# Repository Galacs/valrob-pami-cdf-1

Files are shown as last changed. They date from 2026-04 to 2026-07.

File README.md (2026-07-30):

# Carte Pami CDF 1

Pami integrated circuit board with dual silent stepper driver and ToF sensor

## IC List

- ESP32-S3FH4R2 (Main MCU)
- LDL212 (MCU 3v3 LDO)
- BQ77905 (battery protection)
- WS2812B (RGB addressable led)
- MLT-5020 (buzzer)
- VL53L0X (ToF ranging sensor)
- 2x TMC2209 (Silent 3A stepper driver)

## Top preview

## Preview 3d render

## Pictures

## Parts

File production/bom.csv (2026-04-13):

Designator | Footprint | Quantity | Value | LCSC Part #
AE1 | Johanson_2450AT18x100 | 1 | Antenna | C127629
BZ1 | MagneticBuzzer_Huaneng_MLT-5020 | 1 | Buzzer | C94598
C1, C14, C15, C16, C17, C2, C49, C50 | 0805 | 8 | 10u | C440198
C10, C12, C20, C26, C27, C29, C3, C30, C31, C4, C47, C48, C5, C6, C7, C8, C9 | 0402 | 17 | 0u1 | C307331
C11, C13, C24, C28, C32, C33, C53, C54 | 0402 | 8 | 1u | C52923
C18, C19 | 0402 | 2 | 12p | C1547
C21, C34, C35, C37 | 0402 | 4 | 4u7 | C23733
C22, C23 | 0402 | 2 | 1p2 | C76899
C25 | 0402 | 1 | 10u | C15525
C36, C42 | 0402 | 2 | 22n | C1532
C39, C45 | CP_Elec_6.3x7.7 | 2 | 100u | C165974
D1 | LED_WS2812B_PLCC4_5.0x5.0mm_P3.2mm | 1 | WS2812B | C2874885
D10 | D_SOD-323 | 1 | 100 | C2128
D11 | D_SOD-123 | 1 | 16 | C19077429
D12, D13 | 0805 | 2 | GREEN | C2297
D14 | 0603 | 1 | WHITE | C2290
D15 | D_SOD-123 | 1 | BZT52B3V3 | C19077392
D3, D4, D6, D8 | Diode_DFN1006 | 4 | H5VU10U | C22395519
D5, D9 | D_SMA | 2 | D_Schottky | C22452
J2 | USB_C_Receptacle_HRO_TYPE-C-31-M-12 | 1 | USB_C_Receptacle_USB2.0_14P | C393939
J3 | AMASS_XT30PW-M_1x02_P2.50mm_Horizontal | 1 | Conn_01x02 | C431092
J5 | PinHeader_2x03_P2.54mm_Vertical | 1 | Conn_01x06
L1 | L_Sunlord_MWSA0402S | 1 | 3u3 | C167207
L2 | 0402 | 1 | 24n | C167472
L3 | 0402 | 1 | 6n8 | C77110
L5, L6 | 0402 | 2 | 2n7 | C77108
Q1, Q2 | Vishay_PowerPAK_1212-8_Single | 2 | Q_NMOS | C111309
Q3 | SOT-323_SC-70 | 1 | Q_NMOS | C28646265
R1, R2, R36, R5, R7 | 0402 | 5 | 1k | C11702
R10 | 0402 | 1 | 52k3 | C26982
R11, R14, R16, R17, R27, R29, R31, R34, R35, R40, R41, R42 | 0402 | 12 | 10k | C25744
R12, R22 | 0603 | 2 | 470k | C23178
R13, R20 | 0402 | 2 | 1M | C26083
R15, R18, R23, R25, R26, R3, R4 | 0402 | 7 | 5k1 | C25905
R19 | 0603 | 1 | 3M | C23156
R21 | 0402 | 1 | 510 | C25123
R24 | 0402 | 1 | 0 | C17168
R28 | 0603 | 1 | 1k8 | C4177
R30 | 0402 | 1 | 470 | C25117
R32, R33 | 0402 | 2 | 22 | C25092
R6, R9 | 0402 | 2 | 100 | C25076
R8 | 1206 | 1 | 10m/1W | C105362
SW2 | JST_XH_B2B-XH-A_1x02_P2.50mm_Vertical | 1 | SW_Push | C158012
SW3, SW4 | SW_SPST_TS-1088-xR020 | 2 | SW_Push | C720477
U1 | SOT-583-8 | 1 | TPS62933 | C3200405
U2 | TSSOP-20_4.4x6.5mm_P0.65mm | 1 | BQ77905 | C2866527
U3 | ST_VL53L1x | 1 | VL53L0CXV0DH1 | C91199
U4 | QFN-56-1EP_7x7mm_P0.4mm_EP4x4mm_ThermalVias | 1 | ESP32-S3FN8 | C3013940
U5 | DFN-6-1EP_2x2mm_P0.5mm_ST | 1 | LDL212PV33R | C2969892
U8, U9 | VQFN-28-1EP_5x5mm_P0.5mm_EP3.7x3.7mm_ThermalVias | 2 | TMC2209-LA | C2150710
Y1 | Crystal_SMD_2016-4Pin_2.0x1.6mm | 1 | 48M | C7206306

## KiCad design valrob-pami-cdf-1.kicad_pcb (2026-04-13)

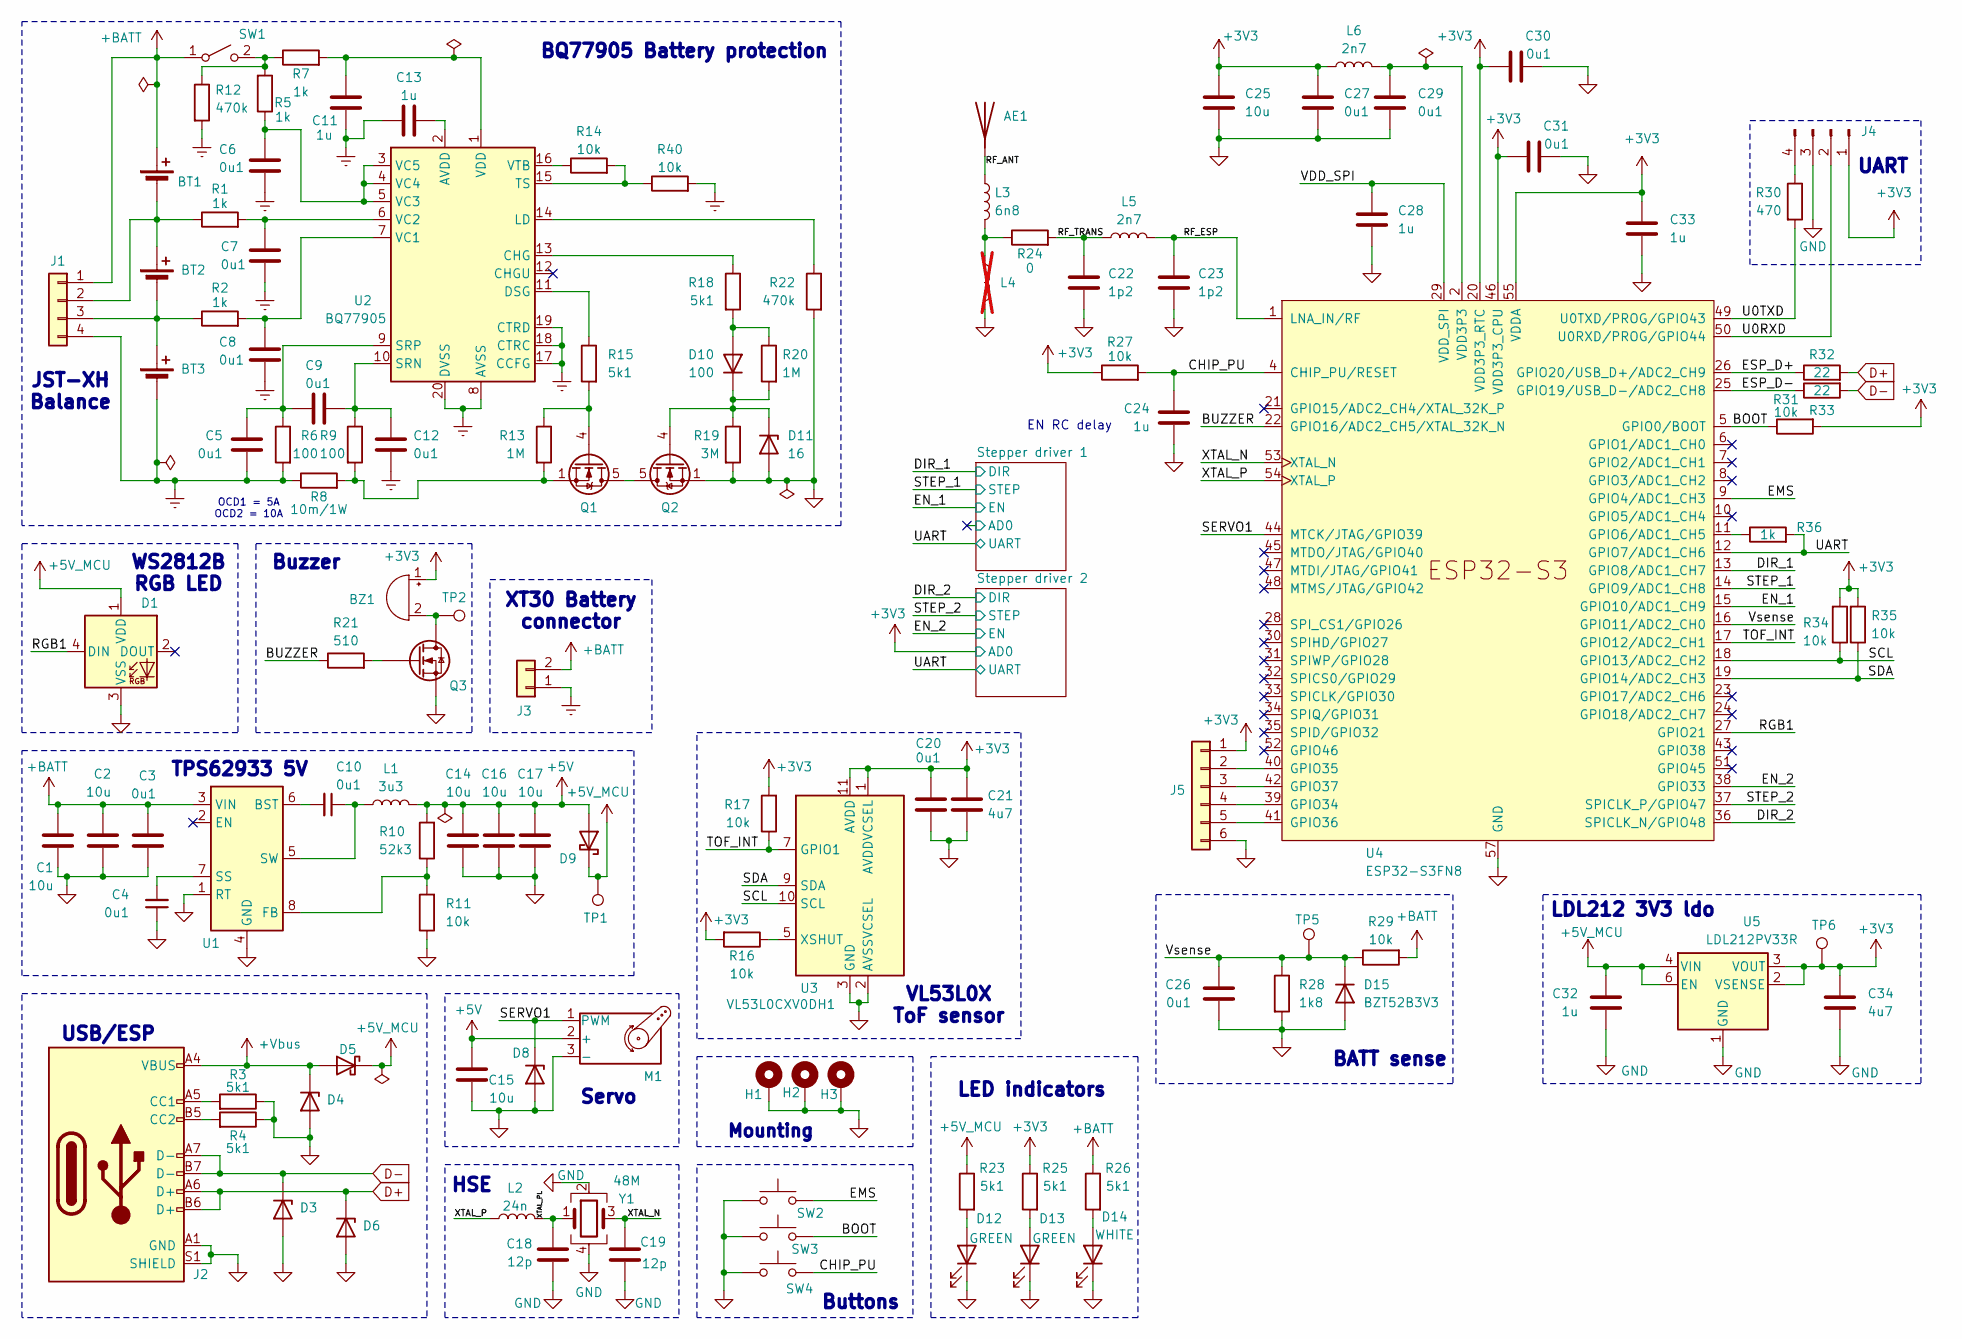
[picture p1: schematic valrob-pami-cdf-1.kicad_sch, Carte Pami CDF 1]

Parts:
AE1: Antenna; Johanson_2450AT18x100; Manufacturer Part Number RFANT3216120A5T; JLCPCB Part # C127629
BT1, BT2, BT3: Battery_Cell
BZ1: Buzzer; MagneticBuzzer_Huaneng_MLT-5020; Manufacturer Part Number MLT-5020; JLCPCB Part # C94598
C1, C2, C14, C15, C16, C17: 10u; C_0805_2012Metric; Manufacturer Part Number GRM21BR61H106KE43L; JLCPCB Part # C440198
C3, C4, C5, C6, C7, C8, C9, C10, C12, C20, C26, C27, C29, C30, C31: 0u1; C_0402_1005Metric; Manufacturer Part Number CL05B104KB54PNC; JLCPCB Part # C307331
C11, C13, C24, C28, C32, C33: 1u; C_0402_1005Metric; Manufacturer Part Number CL05A105KA5NQNC; JLCPCB Part # C52923
C18, C19: 12p; C_0402_1005Metric; Manufacturer Part Number 0402CG120J500NT; JLCPCB Part # C1547
C21, C34: 4u7; C_0402_1005Metric; Manufacturer Part Number CL05A475MP5NRNC; JLCPCB Part # C23733
C22, C23: 1p2; C_0402_1005Metric; Manufacturer Part Number GJM1555C1H1R2WB01D; JLCPCB Part # C76899
C25: 10u; C_0402_1005Metric; Manufacturer Part Number CL05A106MQ5NUNC; JLCPCB Part # C15525
D1: WS2812B; LED_WS2812B_PLCC4_5.0x5.0mm_P3.2mm; Manufacturer Part Number WS2812B-V5/W; JLCPCB Part # C2874885
D3, D4, D6, D8: H5VU10U; Diode_DFN1006; Manufacturer Part Number H5VU10U; JLCPCB Part # C22395519
D5, D9: D_Schottky; D_SMA; Manufacturer Part Number SS54; JLCPCB Part # C22452
D10: 100; D_SOD-323; Manufacturer Part Number 1N4148WS; JLCPCB Part # C2128
D11: 16; D_SOD-123; Manufacturer Part Number MMSZ5246B; JLCPCB Part # C19077429
D12, D13: GREEN; LED_0805_2012Metric; Manufacturer Part Number KT-0805G; JLCPCB Part # C2297
D14: WHITE; LED_0603_1608Metric; Manufacturer Part Number KT-0603W; JLCPCB Part # C2290
D15: BZT52B3V3; D_SOD-123; Manufacturer Part Number BZT52B3V3; JLCPCB Part # C19077392
H1, H2, H3: MountingHole_Pad; MountingHole_2.2mm_M2_Pad_Via
J1: Conn_01x04; JST_XH_S4B-XH-A_1x04_P2.50mm_Horizontal
J2: USB_C_Receptacle_USB2.0_14P; USB_C_Receptacle_HRO_TYPE-C-31-M-12; Manufacturer Part Number TYPE-C16PIN; JLCPCB Part # C393939
J3: Conn_01x02; AMASS_XT30PW-M_1x02_P2.50mm_Horizontal; Manufacturer Part Number XT30PW-M30.G.Y; JLCPCB Part # C431092
J4: Conn_01x04_Pin; PinHeader_1x04_P2.54mm_Vertical
J5: Conn_01x06; PinHeader_2x03_P2.54mm_Vertical
L1: 3u3; L_Sunlord_MWSA0402S; Manufacturer Part Number FXL0420-3R3-M; JLCPCB Part # C167207
L2: 24n; L_0402_1005Metric; Manufacturer Part Number LQW15AN24NG00D; JLCPCB Part # C167472
L3: 6n8; L_0402_1005Metric; Manufacturer Part Number LQG15HS6N8J02D; JLCPCB Part # C77110
L4: L; L_0402_1005Metric; not fitted
L5, L6: 2n7; L_0402_1005Metric; Manufacturer Part Number LQG15HS2N7S02D; JLCPCB Part # C77108
M1: Motor_Servo; PinHeader_1x03_P2.54mm_Horizontal
Q1, Q2: Q_NMOS; Vishay_PowerPAK_1212-8_Single; Manufacturer Part Number SIS412DN-T1-GE3; JLCPCB Part # C111309
Q3: Q_NMOS; SOT-323_SC-70; Manufacturer Part Number BSS138W; JLCPCB Part # C28646265
R1, R2, R5, R7, R36: 1k; R_0402_1005Metric; Manufacturer Part Number 0402WGF1001TCE; JLCPCB Part # C11702
R3, R4, R15, R18, R23, R25, R26: 5k1; R_0402_1005Metric; Manufacturer Part Number 0402WGF5101TCE; JLCPCB Part # C25905
R6, R9: 100; R_0402_1005Metric; Manufacturer Part Number 0402WGF1000TCE; JLCPCB Part # C25076
R8: 10m/1W; R_1206_3216Metric; Manufacturer Part Number FMF06FTHR010-LH; JLCPCB Part # C105362
R10: 52k3; R_0402_1005Metric; Manufacturer Part Number 0402WGF5232TCE; JLCPCB Part # C26982
R11, R14, R16, R17, R27, R29, R31, R34, R35, R40: 10k; R_0402_1005Metric; Manufacturer Part Number 0402WGF1002TCE; JLCPCB Part # C25744
R12, R22: 470k; R_0603_1608Metric; Manufacturer Part Number 0603WAF4703T5E; JLCPCB Part # C23178
R13, R20: 1M; R_0402_1005Metric; Manufacturer Part Number 0402WGF1004TCE; JLCPCB Part # C26083
R19: 3M; R_0603_1608Metric; Manufacturer Part Number 0603WAF3004T5E; JLCPCB Part # C23156
R21: 510; R_0402_1005Metric; Manufacturer Part Number 0402WGF5100TCE; JLCPCB Part # C25123
R24: 0; R_0402_1005Metric; Manufacturer Part Number 0402WGF0000TCE; JLCPCB Part # C17168
R28: 1k8; R_0603_1608Metric; Manufacturer Part Number 0603WAF1801T5E; JLCPCB Part # C4177
R30: 470; R_0402_1005Metric; Manufacturer Part Number 0402WGF4700TCE; JLCPCB Part # C25117
R32, R33: 22; R_0402_1005Metric; Manufacturer Part Number 0402WGF220JTCE; JLCPCB Part # C25092
SW1: SW_SPST; PinHeader_1x02_P2.54mm_Vertical
SW2: SW_Push; JST_XH_B2B-XH-A_1x02_P2.50mm_Vertical; Manufacturer Part Number B2B-XH-A(LF)(SN); JLCPCB Part # C158012
SW3, SW4: SW_Push; SW_SPST_TS-1088-xR020; Manufacturer Part Number TS-1088-AR02016; JLCPCB Part # C720477
TP1, TP2, TP5, TP6: TestPoint; TestPoint_Pad_D2.0mm
U1: TPS62933; SOT-583-8; Manufacturer Part Number TPS62933DRLR; JLCPCB Part # C3200405
U2: BQ77905; TSSOP-20_4.4x6.5mm_P0.65mm; Manufacturer Part Number BQ7790509PWR; JLCPCB Part # C2866527
U3: VL53L0CXV0DH1; ST_VL53L1x; Manufacturer Part Number VL53L0CXV0DH/1; JLCPCB Part # C91199
U4: ESP32-S3FN8; QFN-56-1EP_7x7mm_P0.4mm_EP4x4mm_ThermalVias; Manufacturer Part Number ESP32-S3FH4R2; JLCPCB Part # C3013940
U5: LDL212PV33R; DFN-6-1EP_2x2mm_P0.5mm_ST; Manufacturer Part Number LDL212PV33R; JLCPCB Part # C2969892
Y1: 48M; Crystal_SMD_2016-4Pin_2.0x1.6mm; Manufacturer Part Number R940000096; JLCPCB Part # C7206306

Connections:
+3V3: BZ1.1 (+), C20.1, C21.1, C25.1, C27.1, C30.1, C31.1, C33.1, C34.1, J4.1, J5.1, L6.1, R16.2, R17.2, R25.1, R27.1, R31.2, R34.2, R35.2, TP6.1 (1_1), U3.1 (AVDDVCSEL), U3.11 (AVDD), U4.20 (VDD3P3_RTC), U4.46 (VDD3P3_CPU), U4.55 (VDDA), U4.56 (VDDA), U5.2 (VSENSE), U5.3 (VOUT); also elsewhere on the board
+5V: C14.1, C15.1, C16.1, C17.1, D9.2 (A), L1.2, M1.2 (+), R10.2
+5V_MCU: C32.1, D1.1 (VDD), D5.1 (K), D9.1 (K), R23.1, TP1.1 (1_1), U5.4 (VIN), U5.6 (EN)
+BATT: BT1.1 (+), C1.1, C2.1, C3.1, J1.1, J3.2, R26.1, R29.2, SW1.1 (A), U1.3 (VIN); also elsewhere on the board
+Vbus: D4.1 (K), D5.2 (A), J2.A4 (VBUS), J2.A9 (VBUS), J2.B4 (VBUS), J2.B9 (VBUS)
/BOOT: R31.1, SW3.2, U4.5 (GPIO0/BOOT)
/BUZZER: R21.1, U4.22 (GPIO16/ADC2_CH5/XTAL_32K_N)
/CHIP_PU: C24.1, R27.2, SW4.2, U4.4 (CHIP_PU/RESET)
/DIR_1: U4.13 (GPIO8/ADC1_CH7); also elsewhere on the board
/DIR_2: U4.36 (SPICLK_N/GPIO48); also elsewhere on the board
/EMS: SW2.2, U4.9 (GPIO4/ADC1_CH3)
/EN_1: U4.15 (GPIO10/ADC1_CH9); also elsewhere on the board
/EN_2: U4.38 (GPIO33); also elsewhere on the board
/ESP_D+: R32.1, U4.26 (GPIO20/USB_D+/ADC2_CH9)
/ESP_D-: R33.1, U4.25 (GPIO19/USB_D-/ADC2_CH8)
/RF_ANT: AE1.1 (A_1), L3.1
/RF_ESP: C23.1, L5.2, U4.1 (LNA_IN/RF)
/RF_TRANS: C22.1, L5.1, R24.2
/RGB1: D1.4 (DIN), U4.27 (GPIO21)
/SCL: R34.1, U3.10 (SCL), U4.18 (GPIO13/ADC2_CH2)
/SDA: R35.1, U3.9 (SDA), U4.19 (GPIO14/ADC2_CH3)
/SERVO1: D8.1 (K), M1.1 (PWM), U4.44 (MTCK/JTAG/GPIO39)
/STEP_1: U4.14 (GPIO9/ADC1_CH8); also elsewhere on the board
/STEP_2: U4.37 (SPICLK_P/GPIO47); also elsewhere on the board
/TOF_INT: R17.1, U3.7 (GPIO1), U4.17 (GPIO12/ADC2_CH1)
/U0RXD: J4.2, U4.50 (U0RXD/PROG/GPIO44)
/U0TXD: R30.2, U4.49 (U0TXD/PROG/GPIO43)
/UART: R36.2, U4.12 (GPIO7/ADC1_CH6); also elsewhere on the board
/VDD_SPI: C28.1, U4.29 (VDD_SPI)
/Vsense: C26.1, D15.1 (K), R28.1, R29.1, TP5.1 (1_1), U4.16 (GPIO11/ADC2_CH0)
/XTAL_N: C19.1, U4.53 (XTAL_N), Y1.3
/XTAL_P: L2.1, U4.54 (XTAL_P)
/XTAL_PL: C18.2, L2.2, Y1.1
BGND: BT3.2 (-), C5.2, C6.2, C7.2, C8.2, C11.1, C12.2, C13.2, J1.4, J3.1, R6.2, R8.1, R12.2, R40.2, U2.8 (AVSS), U2.17 (CCFG), U2.18 (CTRC), U2.19 (CTRD), U2.20 (DVSS)
D+: D6.1 (K), J2.A6 (D+), J2.B6 (D+), R32.2
D-: D3.1 (K), J2.A7 (D-), J2.B7 (D-), R33.2
GND: C1.2, C2.2, C3.2, C4.1, C14.2, C15.2, C16.2, C17.2, C18.1, C19.2, C20.2, C21.2, C22.2, C23.2, C24.2, C25.2, C26.2, C27.2, C28.2, C29.2, C30.2, C31.2, C32.2, C33.2, C34.2, D1.3 (VSS), D3.2 (A), D4.2 (A), D6.2 (A), D8.2 (A), D11.2 (A), D12.1 (K), D13.1 (K), D14.1 (K), D15.2 (A), H1.1 (1_1), H2.1 (1_1), H3.1 (1_1), J2.A1 (GND), J2.A12 (GND), J2.B1 (GND), J2.B12 (GND), J2.S1 (SHIELD), J4.3, J5.6, L4.2, M1.3 (-), Q2.1 (S), Q2.2 (S), Q2.3 (S), Q3.2 (S), R3.1, R4.1, R11.1, R19.2, R22.2, R28.2, SW2.1, SW3.1, SW4.1, U1.1 (RT), U1.4 (GND), U3.2 (AVSSVCSEL), U3.3 (GND), U3.4 (GND), U3.6 (GND), U3.12 (GND), U4.57 (GND), U5.1 (GND), Y1.2, Y1.4; also elsewhere on the board
unnamed: BZ1.2 (-), Q3.3 (D), TP2.1 (1_1)
unnamed: D10.2 (A), R18.2, R20.1
unnamed: D10.1 (K), D11.1 (K), Q2.4 (G), R19.1, R20.2
unnamed: D12.2 (A), R23.2
unnamed: D13.2 (A), R25.2
unnamed: D14.2 (A), R26.2
unnamed: BT1.2 (-), BT2.1 (+), J1.2, R1.1
unnamed: BT2.2 (-), BT3.1 (+), J1.3, R2.1
unnamed: J2.A5 (CC1), R3.2
unnamed: J2.B5 (CC2), R4.2
unnamed: J4.4, R30.1
unnamed: J5.2, U4.40 (GPIO35)
unnamed: J5.3, U4.42 (GPIO37)
unnamed: J5.4, U4.39 (GPIO34)
unnamed: J5.5, U4.41 (GPIO36)
unnamed: L3.2, L4.1, R24.1
unnamed: Q1.5 (D), Q2.5 (D)
unnamed: Q1.4 (G), R13.1, R15.2
unnamed: Q1.1 (S), Q1.2 (S), Q1.3 (S), R8.2, R9.2, R13.2
unnamed: Q3.1 (G), R21.2
unnamed: R5.2, R7.1, R12.1, SW1.2 (B)
unnamed: C10.2, U1.6 (BST)
unnamed: R10.1, R11.2, U1.8 (FB)
unnamed: C4.2, U1.7 (SS)
unnamed: C10.1, L1.1, U1.5 (SW)
unnamed: C13.1, U2.2 (AVDD)
unnamed: R18.1, U2.13 (CHG)
unnamed: R15.1, U2.11 (DSG)
unnamed: R22.1, U2.14 (LD)
unnamed: C9.1, C12.1, R9.1, U2.10 (SRN)
unnamed: C5.1, C9.2, R6.1, U2.9 (SRP)
unnamed: R14.2, R40.1, U2.15 (TS)
unnamed: C8.1, R2.2, U2.7 (VC1)
unnamed: C7.1, R1.2, U2.6 (VC2)
unnamed: C6.1, R5.1, U2.3 (VC5), U2.4 (VC4), U2.5 (VC3)
unnamed: C11.2, R7.2, U2.1 (VDD)
unnamed: R14.1, U2.16 (VTB)
unnamed: R16.1, U3.5 (XSHUT)
unnamed: R36.1, U4.11 (GPIO6/ADC1_CH5)
VDD3P3: C29.1, L6.2, U4.2 (VDD3P3), U4.3 (VDD3P3)

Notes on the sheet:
UART
Buttons
LDL212 3V3 ldo
OCD1 = 5A OCD2 = 10A
JST-XH Balance
BQ77905 Battery protection
Servo
VL53L0X ToF sensor
EN RC delay
BATT sense
WS2812B RGB LED
LED indicators
Buzzer
TPS62933 5V
HSE
USB/ESP
XT30 Battery connector
Mounting

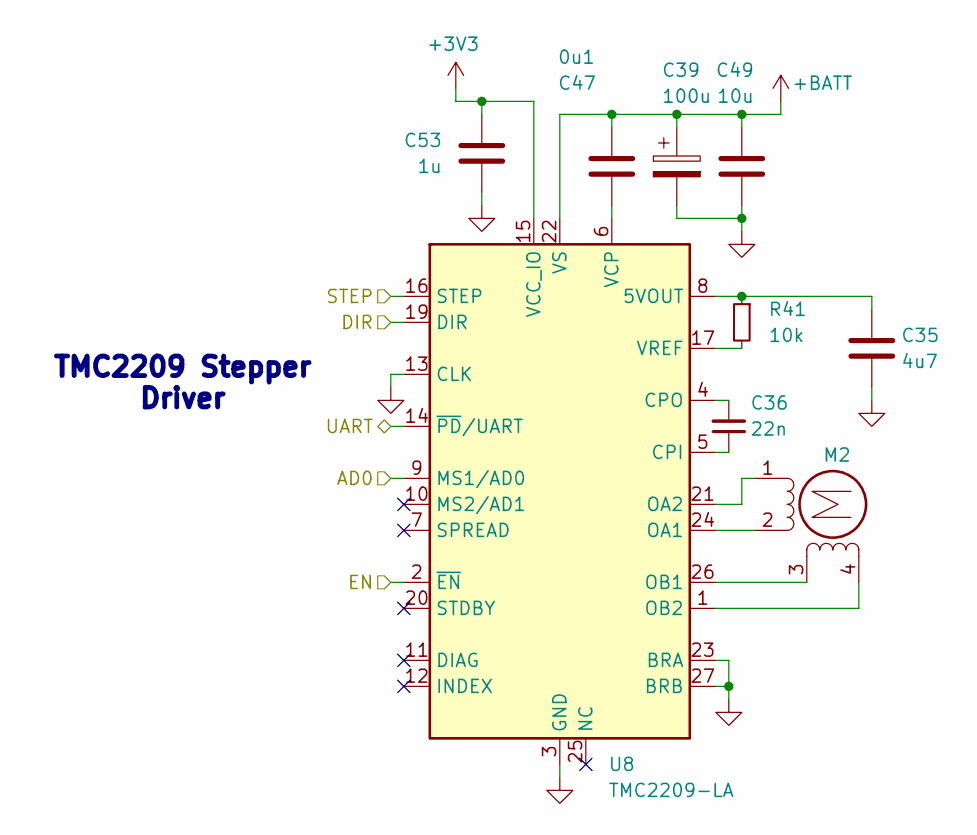
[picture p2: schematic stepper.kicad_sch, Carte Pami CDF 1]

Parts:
C35: 4u7; C_0402_1005Metric; Manufacturer Part Number CL05A475MP5NRNC; JLCPCB Part # C23733
C36: 22n; C_0402_1005Metric; Manufacturer Part Number 0402B223K500NT; JLCPCB Part # C1532
C39: 100u; CP_Elec_6.3x7.7; Manufacturer Part Number EEEFTH101XAP; JLCPCB Part # C165974
C47: 0u1; C_0402_1005Metric; Manufacturer Part Number CL05B104KB54PNC; JLCPCB Part # C307331
C49: 10u; C_0805_2012Metric; Manufacturer Part Number GRM21BR61H106KE43L; JLCPCB Part # C440198
C53: 1u; C_0402_1005Metric; Manufacturer Part Number CL05A105KA5NQNC; JLCPCB Part # C52923
M2: Stepper_Motor_bipolar; JST_XH_S4B-XH-A_1x04_P2.50mm_Horizontal
R41: 10k; R_0402_1005Metric; Manufacturer Part Number 0402WGF1002TCE; JLCPCB Part # C25744
U8: TMC2209-LA; VQFN-28-1EP_5x5mm_P0.5mm_EP3.7x3.7mm_ThermalVias; Manufacturer Part Number TMC2209-LA-T; JLCPCB Part # C2150710

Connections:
+3V3: C53.1, U8.15 (VCC_IO); also elsewhere on the board
+BATT: C39.1, C47.1, C49.1, U8.22 (VS), U8.28 (VS); also elsewhere on the board
/DIR_1: U8.19 (DIR); also elsewhere on the board
/EN_1: U8.2 (~EN); also elsewhere on the board
/STEP_1: U8.16 (STEP); also elsewhere on the board
/Stepper driver 1/AD0: U8.9 (MS1/AD0)
/UART: U8.14 (~PD/UART); also elsewhere on the board
GND: C35.2, C39.2, C49.2, C53.2, U8.3 (GND), U8.13 (CLK), U8.18 (GND), U8.23 (BRA), U8.27 (BRB), U8.29 (GND); also elsewhere on the board
unnamed: M2.1 (-_1), U8.21 (OA2)
unnamed: C35.1, R41.1, U8.8 (5VOUT)
unnamed: C36.1, U8.5 (CPI)
unnamed: C36.2, U8.4 (CPO)
unnamed: M2.2, U8.24 (OA1)
unnamed: M2.3, U8.26 (OB1)
unnamed: M2.4, U8.1 (OB2)
unnamed: C47.2, U8.6 (VCP)
unnamed: R41.2, U8.17 (VREF)

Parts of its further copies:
C37: 4u7; C_0402_1005Metric; Manufacturer Part Number CL05A475MP5NRNC; JLCPCB Part # C23733
C42: 22n; C_0402_1005Metric; Manufacturer Part Number 0402B223K500NT; JLCPCB Part # C1532
C45: 100u; CP_Elec_6.3x7.7; Manufacturer Part Number EEEFTH101XAP; JLCPCB Part # C165974
C48: 0u1; C_0402_1005Metric; Manufacturer Part Number CL05B104KB54PNC; JLCPCB Part # C307331
C50: 10u; C_0805_2012Metric; Manufacturer Part Number GRM21BR61H106KE43L; JLCPCB Part # C440198
C54: 1u; C_0402_1005Metric; Manufacturer Part Number CL05A105KA5NQNC; JLCPCB Part # C52923
M3: Stepper_Motor_bipolar; JST_XH_S4B-XH-A_1x04_P2.50mm_Horizontal
R42: 10k; R_0402_1005Metric; Manufacturer Part Number 0402WGF1002TCE; JLCPCB Part # C25744
U9: TMC2209-LA; VQFN-28-1EP_5x5mm_P0.5mm_EP3.7x3.7mm_ThermalVias; Manufacturer Part Number TMC2209-LA-T; JLCPCB Part # C2150710

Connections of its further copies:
+3V3: C54.1, U9.9 (MS1/AD0), U9.15 (VCC_IO); also elsewhere on the board
+BATT: C45.1, C48.1, C50.1, U9.22 (VS), U9.28 (VS); also elsewhere on the board
/DIR_2: U9.19 (DIR); also elsewhere on the board
/EN_2: U9.2 (~EN); also elsewhere on the board
/STEP_2: U9.16 (STEP); also elsewhere on the board
/UART: U9.14 (~PD/UART); also elsewhere on the board
GND: C37.2, C45.2, C50.2, C54.2, U9.3 (GND), U9.13 (CLK), U9.18 (GND), U9.23 (BRA), U9.27 (BRB), U9.29 (GND); also elsewhere on the board
unnamed: M3.1 (-_1), U9.21 (OA2)
unnamed: C37.1, R42.1, U9.8 (5VOUT)
unnamed: C42.1, U9.5 (CPI)
unnamed: C42.2, U9.4 (CPO)
unnamed: M3.2, U9.24 (OA1)
unnamed: M3.3, U9.26 (OB1)
unnamed: M3.4, U9.1 (OB2)
unnamed: C48.2, U9.6 (VCP)
unnamed: R42.2, U9.17 (VREF)

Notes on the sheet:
TMC2209 Stepper Driver

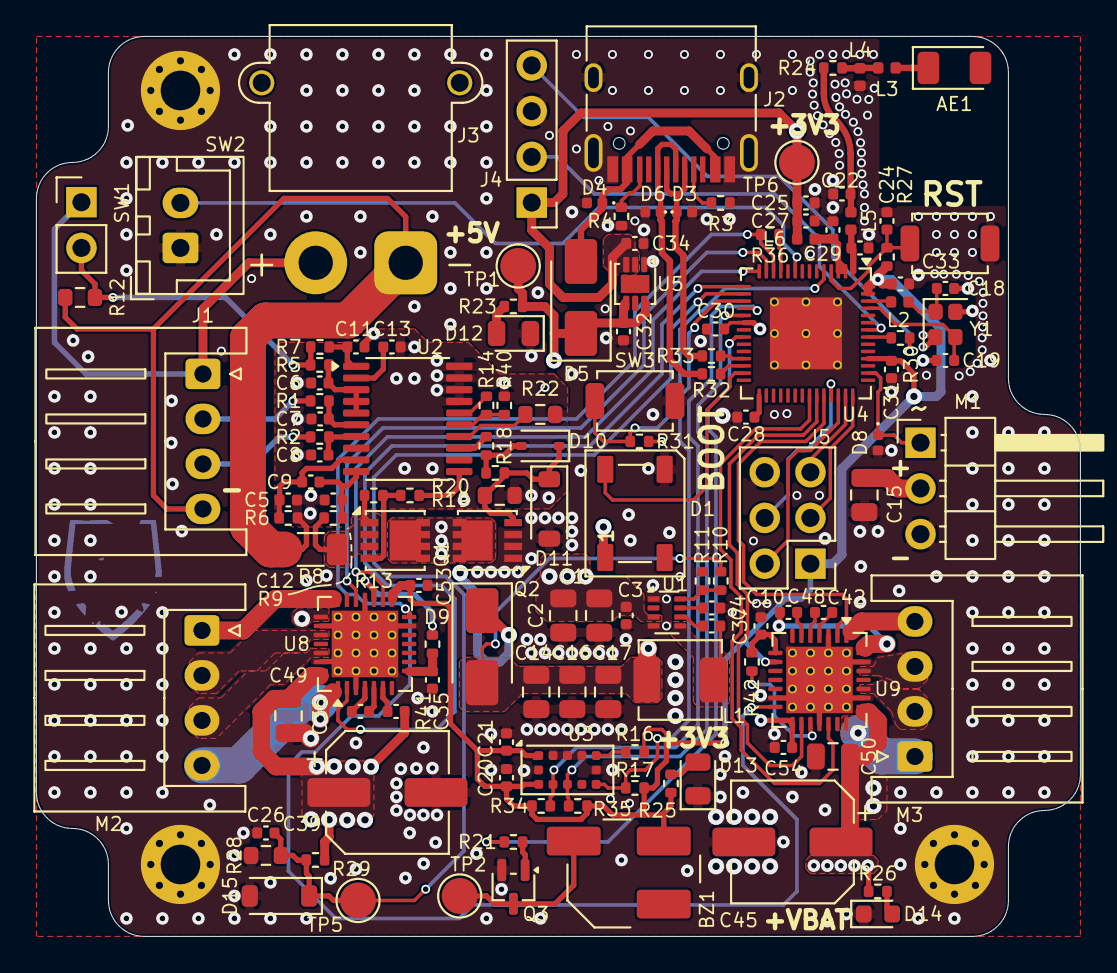
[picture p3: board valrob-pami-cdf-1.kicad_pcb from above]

Board: 4 copper layers, 58.0 x 50.0 mm, 136 parts (0 on the bottom side), 95 nets.

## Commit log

2026-02-16 schem: import esp32-s3 circuit from mhadb-main-board
    [valrob-pami-cdf-1.kicad_sch]
2026-02-16 schem: import HSE crystal
    [valrob-pami-cdf-1.kicad_sch]
2026-02-16 schem: import usbc connector
    [valrob-pami-cdf-1.kicad_sch]
2026-02-16 schem: import LDL212 3V3 ldo
    [valrob-pami-cdf-1.kicad_sch]
2026-02-16 schem: add BOOT and CHIP_PU buttons*
    [valrob-pami-cdf-1.kicad_sch]
2026-02-16 schem: add 3x WS2812B RGB LEDs
    [valrob-pami-cdf-1.kicad_sch]
2026-02-16 schem: add servo connector
    [valrob-pami-cdf-1.kicad_sch]
2026-02-16 schem: import BQ77905 Battery protection
    [valrob-pami-cdf-1.kicad_sch]
2026-02-16 schem: import buzzer
    [valrob-pami-cdf-1.kicad_sch]
2026-02-16 schem: add XT30 battery connector
    [valrob-pami-cdf-1.kicad_sch]
2026-02-16 pcb: add indicator leds
    [valrob-pami-cdf-1.kicad_sch]
2026-02-16 schem: add BQ77905 enable pull down resistor
    [valrob-pami-cdf-1.kicad_sch]
2026-02-16 schem: import DRV8424 stepper driver and reorganize
    [stepper.kicad_sch, valrob-pami-cdf-1.kicad_sch]
2026-02-16 schem: add placeholder TPS56A37 5V smps
    [valrob-pami-cdf-1.kicad_sch]
2026-02-16 schem: import BATT sense from valrob-alim
    [valrob-pami-cdf-1.kicad_sch]
2026-02-18 schem: add missing rgb leds ground symbol
    [valrob-pami-cdf-1.kicad_sch]
2026-02-20 schem: set stepper driver microstepping and decay config
    [stepper.kicad_sch]
2026-02-20 schem: change stepper driver connector
    [stepper.kicad_sch]
2026-02-20 schem: fix stepper hierachical sheets
    [stepper.kicad_sch, valrob-pami-cdf-1.kicad_sch]
2026-02-21 schem: change buck converter to TPS62933 5V
    [valrob-pami-cdf-1.kicad_sch]
2026-02-21 schem: add VL53L0x tof sensor
    [valrob-pami-cdf-1.kicad_sch]
2026-02-22 schem: add EMS button
    [valrob-pami-cdf-1.kicad_sch]
2026-02-22 schem: add mounting holes
    [valrob-pami-cdf-1.kicad_sch]
2026-02-22 schem: connecto all gpios to mcu
    [stepper.kicad_sch, valrob-pami-cdf-1.kicad_sch]
2026-02-22 schem: add test points
    [valrob-pami-cdf-1.kicad_sch]
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2026-02-22 schem: run and fix ERC
    [valrob-pami-cdf-1.kicad_sch]
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2026-02-22 schem: fix BOM
    [valrob-pami-cdf-1.kicad_sch]
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2026-02-22 schem: change rgb led 5v rail
    [valrob-pami-cdf-1.kicad_sch]
2026-02-22 pcb: import 4 layer stackup and constraints
    [valrob-pami-cdf-1.kicad_pcb]
2026-02-22 pcb: import components and add missing 3d models
    [valrob-pami-cdf-1.kicad_pcb]
2026-02-22 pcb: add stepper layout
    [stepper.kicad_sch, valrob-pami-cdf-1.kicad_pcb]
2026-02-22 pcb: add usbc layout
    [valrob-pami-cdf-1.kicad_pcb]
2026-02-22 pcb: add initial smps layout
    [valrob-pami-cdf-1.kicad_pcb]
2026-02-22 pcb: add bms layout
    [valrob-pami-cdf-1.kicad_pcb, valrob-pami-cdf-1.kicad_sch]
2026-02-22 pcb: add missing xt30 3d model
    [valrob-pami-cdf-1.kicad_pcb]
2026-02-22 pcb: refine layout and add board outline
    [valrob-pami-cdf-1.kicad_pcb, valrob-pami-cdf-1.kicad_sch]
2026-02-22 schem: update connectors to horizontal footprints
    [stepper.kicad_sch, valrob-pami-cdf-1.kicad_sch]
2026-02-22 schem: update servo connector to horizontal
    [valrob-pami-cdf-1.kicad_sch]
2026-02-22 pcb: change connectors layout
    [valrob-pami-cdf-1.kicad_pcb, valrob-pami-cdf-1.kicad_sch]
2026-02-22 schem: add 6 spare gpio header
    [valrob-pami-cdf-1.kicad_sch]
2026-02-22 pcb: refine board outline
    [valrob-pami-cdf-1.kicad_pcb]
2026-02-22 pcb: add gnd planes
    [valrob-pami-cdf-1.kicad_pcb]
2026-02-22 pcb: add gnd vias
    [valrob-pami-cdf-1.kicad_pcb]
2026-02-22 pcb: add drill/place origin
    [valrob-pami-cdf-1.kicad_pcb]
2026-02-22 schem/pcb: reorganize programmable gpios
    [valrob-pami-cdf-1.kicad_pcb, valrob-pami-cdf-1.kicad_sch]
2026-02-22 pcb: add rf routing
    [valrob-pami-cdf-1.kicad_pcb]
2026-02-22 pcb: add crystal routing
    [valrob-pami-cdf-1.kicad_pcb]
2026-02-22 pcb: add usb routing
    [valrob-pami-cdf-1.kicad_pcb]
2026-02-22 pcb: add uart routing
    [valrob-pami-cdf-1.kicad_pcb]
2026-02-22 pcb: add servo connector routing
    [valrob-pami-cdf-1.kicad_pcb]
2026-02-22 pcb: add smps routing
    [valrob-pami-cdf-1.kicad_pcb]
2026-02-22 pcb: add bms routing
    [valrob-pami-cdf-1.kicad_pcb]
2026-02-22 pcb: add buzzer routing
    [valrob-pami-cdf-1.kicad_pcb]
2026-02-22 pcb: add local stepper drivers routing
    [stepper.kicad_sch, valrob-pami-cdf-1.kicad_pcb, valrob-pami-cdf-1.kicad_sch]
2026-02-22 pcb: add right stepper driver routing
    [valrob-pami-cdf-1.kicad_pcb, valrob-pami-cdf-1.kicad_sch]
2026-02-22 pcb: fix bms BGND pour
    [valrob-pami-cdf-1.kicad_pcb]
2026-02-22 pcb: add tof sensor routing
    [valrob-pami-cdf-1.kicad_pcb, valrob-pami-cdf-1.kicad_sch]
2026-02-22 pcb: add missing stepper drv fault 2 connection
    [valrob-pami-cdf-1.kicad_pcb, valrob-pami-cdf-1.kicad_sch]
2026-02-22 pcb: add left stepper driver routing
    [valrob-pami-cdf-1.kicad_pcb, valrob-pami-cdf-1.kicad_sch]
2026-02-22 pcb: add RGB led routing
    [valrob-pami-cdf-1.kicad_pcb]
2026-02-22 pcb: add spare gpio routing
    [valrob-pami-cdf-1.kicad_pcb, valrob-pami-cdf-1.kicad_sch]
2026-02-22 pcb: fix right stepper drv gnd island
    [valrob-pami-cdf-1.kicad_pcb]
2026-02-22 pcb: add EMS routing
    [valrob-pami-cdf-1.kicad_pcb, valrob-pami-cdf-1.kicad_sch]
2026-02-22 pcb: add +BATT routing
    [valrob-pami-cdf-1.kicad_pcb]
2026-02-22 pcb: add +3V3 pwr routing
    [valrob-pami-cdf-1.kicad_pcb]
2026-02-22 pcb: add 5V pwr routing
    [valrob-pami-cdf-1.kicad_pcb]
2026-02-22 pcb: add +VBUS pwr routing
    [valrob-pami-cdf-1.kicad_pcb]
2026-02-22 pcb: add BOOT routing
    [valrob-pami-cdf-1.kicad_pcb]
2026-02-22 pcb: add VDD_SPI routing
    [valrob-pami-cdf-1.kicad_pcb]
2026-02-22 pcb: add status leds routing
    [valrob-pami-cdf-1.kicad_pcb]
2026-02-22 pcb: fix missing gnd connections
    [valrob-pami-cdf-1.kicad_pcb]
2026-02-22 schem: add no connects
    [valrob-pami-cdf-1.kicad_sch]
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2026-02-23 schem: fix L exclude from BOM
    [valrob-pami-cdf-1.kicad_pcb, valrob-pami-cdf-1.kicad_sch]
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2026-02-23 pcb: run and fix DRC
    [valrob-pami-cdf-1.kicad_pcb]
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2026-04-13 pcb: add missing 3d models
    [valrob-pami-cdf-1.kicad_pcb]
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2026-04-13 schem/pcb: fix stepper driver vcc_io voltage
    [stepper.kicad_sch, valrob-pami-cdf-1.kicad_pcb]
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
